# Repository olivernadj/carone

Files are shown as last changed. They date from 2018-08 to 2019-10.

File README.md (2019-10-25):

# CarOne
Turn a self balancing scooter -Hoverboard- into a kids' electric car.

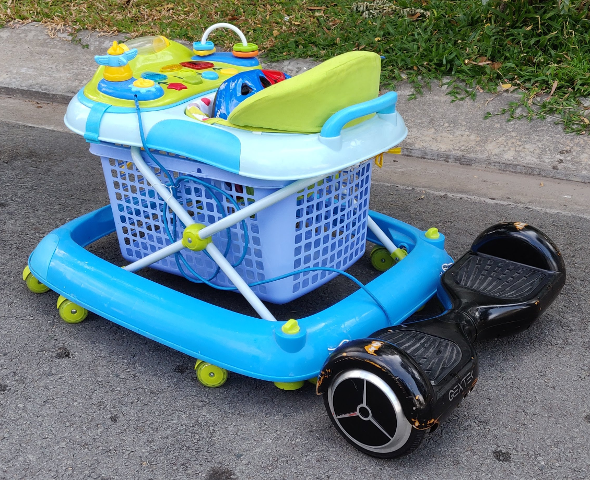
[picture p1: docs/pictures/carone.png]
 

The main goal of the project is to keep the original functionality and behavior of the self balancing scooter, but in the same time with an extension board enable external control. Also use cheap and well know electrical parts and component.

**NOTE: this repo is about to build an Expansion board on top of original Motherboard**
With CarOne Expansion board the max speed you can get is 142cm/s. In case you are not intend to keep the original functionality and you don't mind to replace the firmware and completely re-purpose the hoverboard, I recommend to check this active repo out: https://github.com/NiklasFauth/hoverboard-firmware-hack

## How It Works?
It's follow [Brew's idea][drewsblog] and it hijacks gyro sensor communication between the **Motherboard** and the **Gyro Sensor board**. It sends fake gyro sensor information to **Motherboard**, but also it reads **Hall effect sensor** to detect the speed. 

- [Hardware and wiring](./docs/hardware.md)
- [Board Specification and Applied Units](./docs/specification.md)
- [CarOne glossary](./docs/glossary.md)

## Achievements on Arduino Micro (ATmega328P 16MHz) board.

- [SoftSerialParallelWrite](https://github.com/olivernadj/SoftSerialParallelWrite) for sending parallel UART signal to the Daughterboard.
- Shmitt Trigger in background process.
- [Auto-cruise algorithm](./docs/autocruise.ipynb) development of Auto-cruise algorithm before C implementation.
- All of the above dots in a single board.

## License

    Copyright [2019] [oliver nadj]

    Licensed under the Apache License, Version 2.0 (the "License");
    you may not use this file except in compliance with the License.
    You may obtain a copy of the License at

        http://www.apache.org/licenses/LICENSE-2.0

    Unless required by applicable law or agreed to in writing, software
    distributed under the License is distributed on an "AS IS" BASIS,
    WITHOUT WARRANTIES OR CONDITIONS OF ANY KIND, either express or implied.
    See the License for the specific language governing permissions and
    limitations under the License.

[//]: # (References)
[drewsblog]: http://drewspewsmuse.blogspot.com/2016/06/how-i-hacked-self-balancing-scooter.html

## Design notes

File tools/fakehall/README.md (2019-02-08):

# FakeHall - Fake the hall signal of a hoverboard

Fake the hall project is a testing toll for an other experiment where  I would
like to hijack a hoverboard in a most simple way possible.
It generates fake signal similar to original one, except this use square wave
signal instead of sinusoid one.

## Captured Hall Effect Sensor
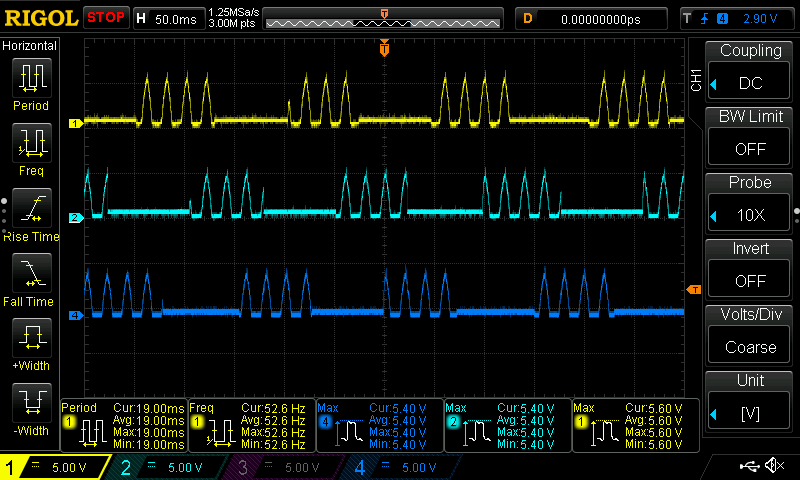
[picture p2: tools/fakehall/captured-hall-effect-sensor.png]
Captured Hall Effect Sensor


## Fake the hall output
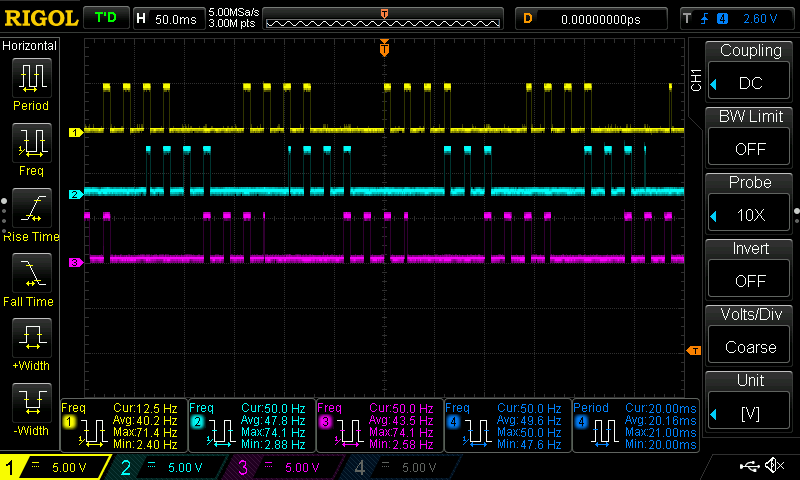
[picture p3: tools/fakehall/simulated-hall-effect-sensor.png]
Fake the hall output


## Demo
IMAGE ALT TEXT HERE (https://youtu.be/ExROV8EL7GM)

## Update
The sinusoid wave come from my broken earth pin in the power strip. What makes the masking features useless.
So I turned the masking features to off by default.

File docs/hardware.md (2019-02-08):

# Hardware and wiring

## Hardware - Expansion Board

### Parts
- 1 x **Arduino Pro Mini** or ATMega328P
- 1 x **LM2596 DC-DC Step Down Buck Converter** Module
- 1 x **74HCT4052N multiplexer** resolver. Can be replaced with discrete logic gates as I did in the earlier version [carone-v3.png](https://raw.githubusercontent.com/olivernadj/carone/master/docs/pictures/carone-v3.png), [data-selector-v3.fzz](https://github.com/olivernadj/carone/raw/master/data-selector-v3.fzz)
- 1 x **AMS1117 3.3 1A Voltage Regulator**
- 4 x 1K, 1 x 10L Resistor
- 2 x 2N2222A NPN Transistor
- 1 x 10nF electrolytic Capacitor
- 4 x 1N4001 Diode - optional

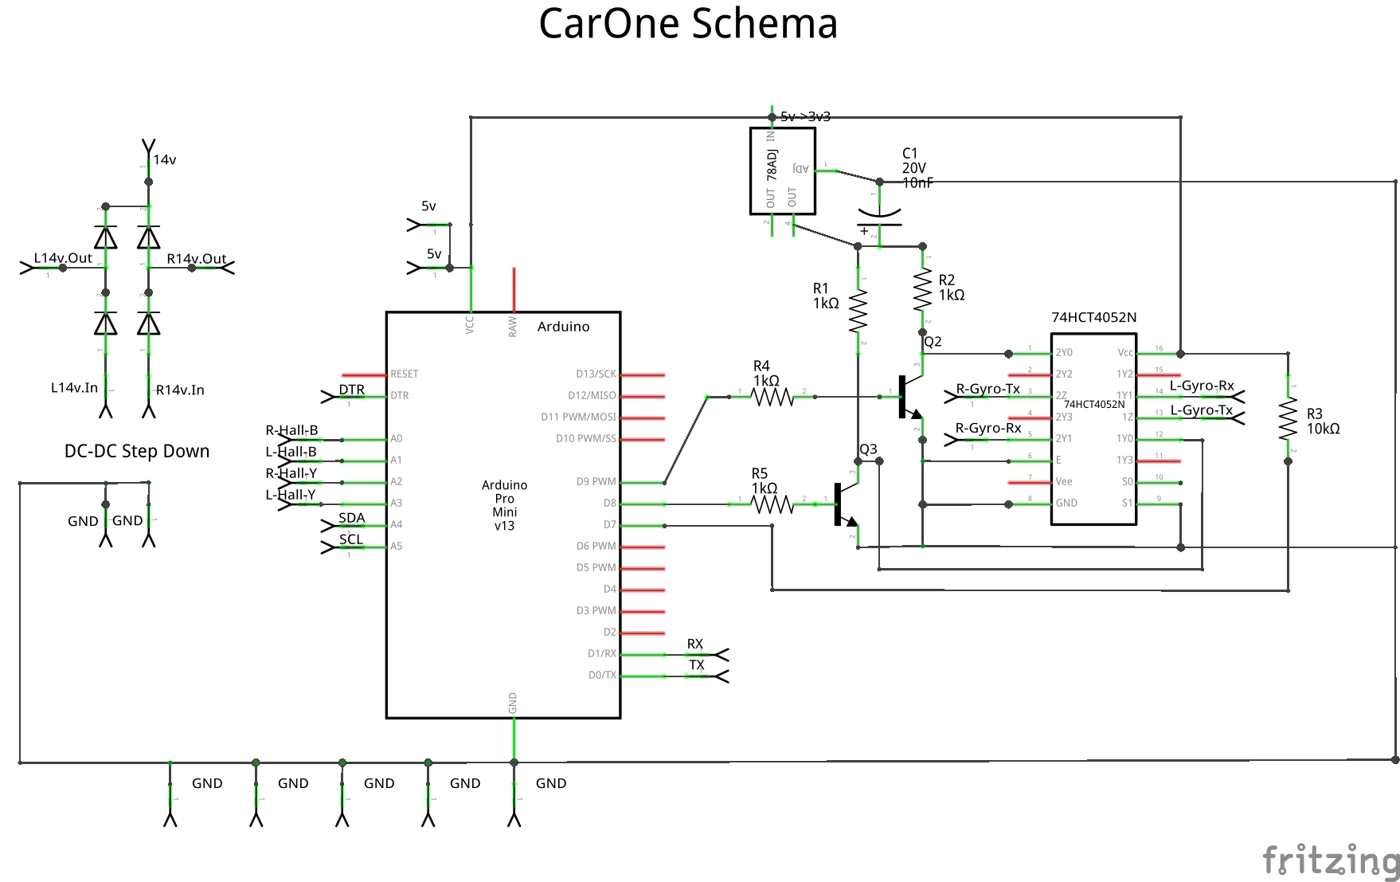
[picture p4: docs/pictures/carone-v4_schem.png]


<p align="center">
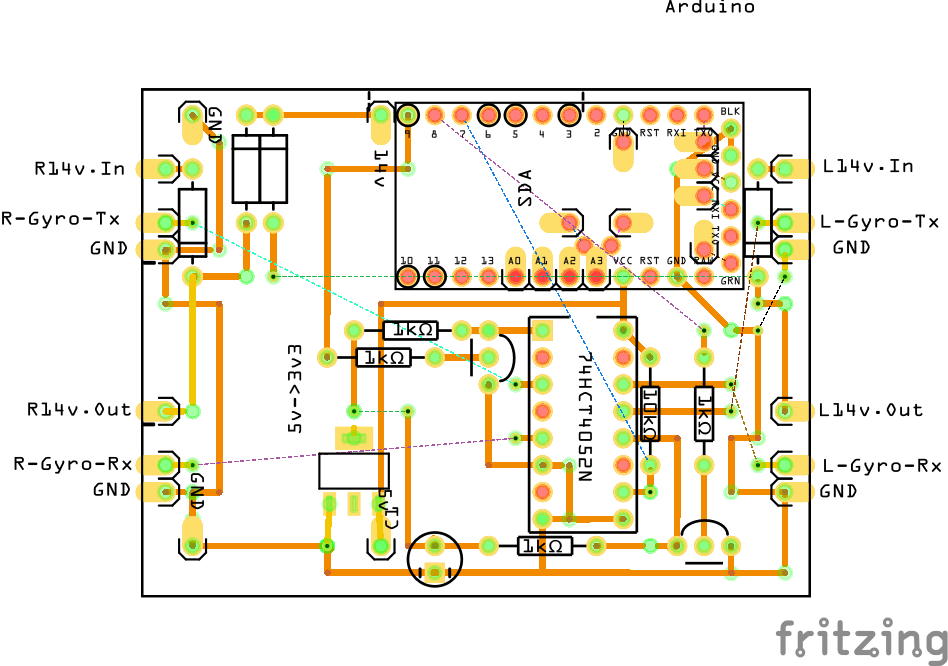
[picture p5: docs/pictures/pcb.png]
  
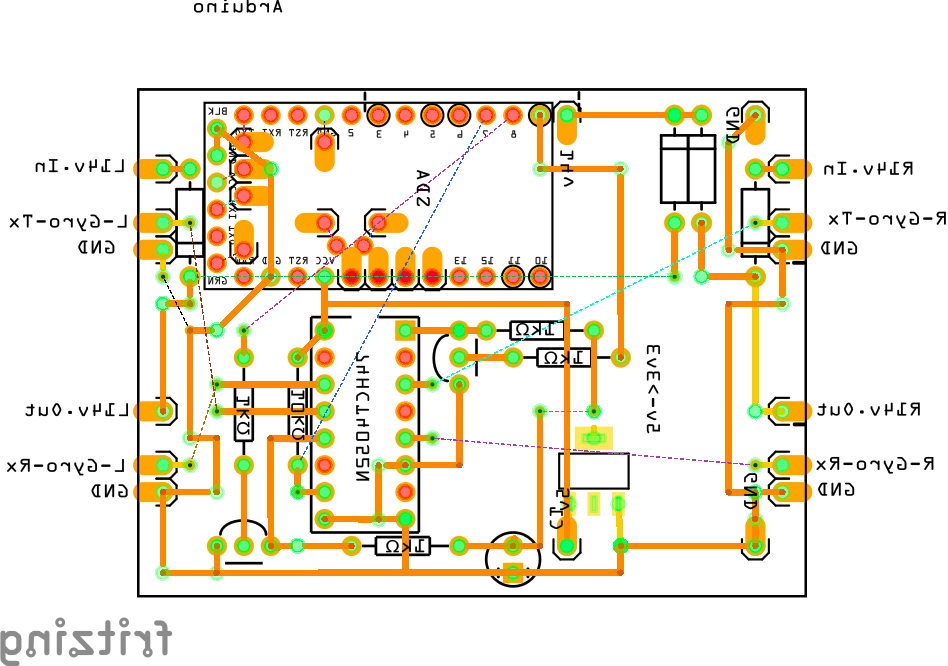
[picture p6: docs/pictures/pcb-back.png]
  
</p>

Check out the Fritzing project file: [carone-v4.fzz](https://github.com/olivernadj/carone/raw/master/carone-v4.fzz)

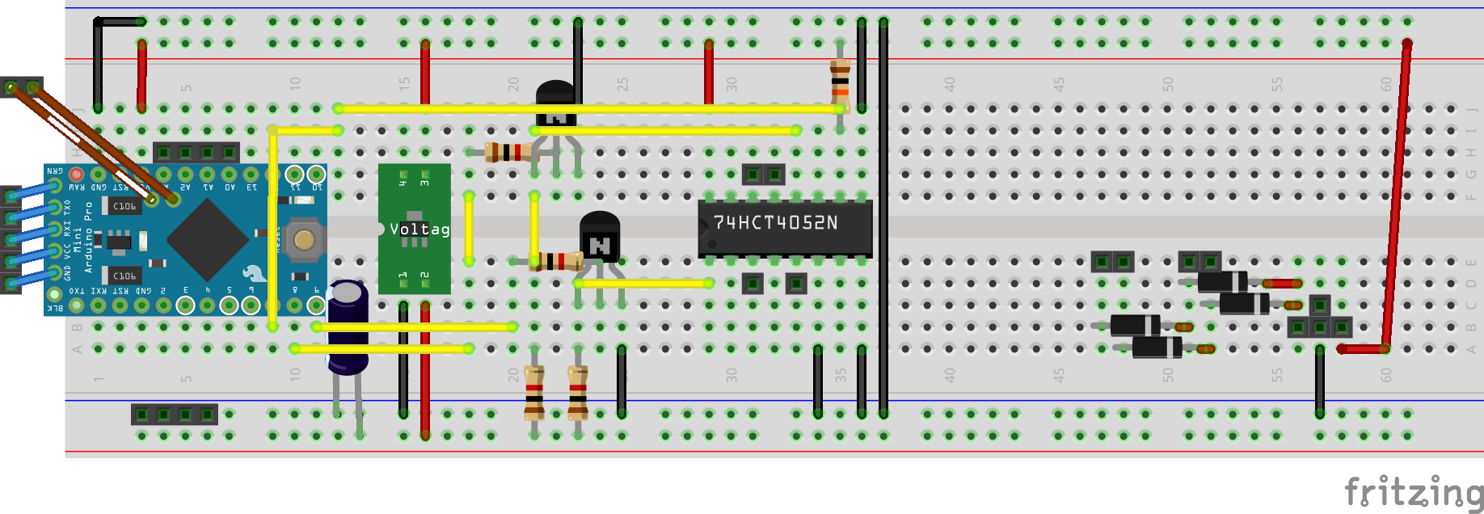
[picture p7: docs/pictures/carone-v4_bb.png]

---

Video: CarOne Expansion Boards Evolution - Try and fail (https://youtu.be/8EtJPLyAzEU)

## How to wire?
The minimum damage you need to do is to cat wires.

<p align="center">
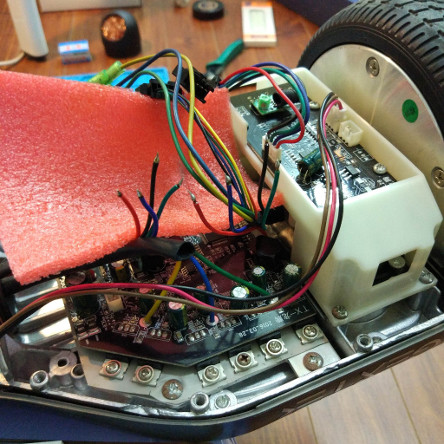
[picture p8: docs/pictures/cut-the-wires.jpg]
  
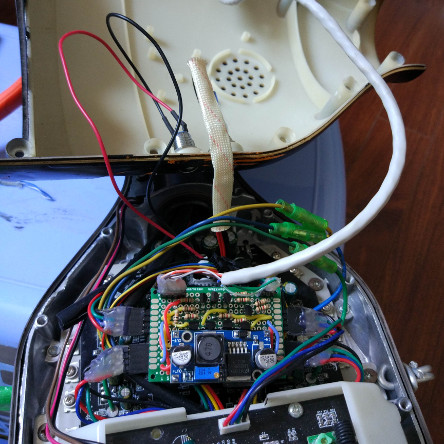
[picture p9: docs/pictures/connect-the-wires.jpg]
  
</p>

Affected wires on both left and right side:
- Hall Yellow and Blue - for speed detection
- Gyro Sensor Red and Black - for power supply to Expansion board
- Gyro Sensor Green - for receiving fake UART from Expansion board

The transmission signal from the Motherboard to Gyro Sensor is untouched.

Abbreviation | Description |  | Abbreviation | Description
--- | --- | --- | --- | ---
**`DTR`** | Arduino Serial Reset | | **`L14v.In`** | Left Red Gyro Sensor from the Motherboard
**`DTR`** | Arduino Serial Reset | | **`R14v.In`** | Right Red Gyro Sensor Red from the Motherboard
**`RX`** | Arduino Serial RX | | **`L14v.Out`** | Left Red Gyro Sensor Red to Gyro Sensor
**`TX`** | Arduino Serial TX | | **`R14v.Out`** | Right Red Gyro Sensor Red to Gyro Sensor
**`L-Hall-B`** | Left Hall Blue - join | | **`L-Gyro-Rx`** | Left Green Gyro Sensor Red from Gyro Sensor
**`L-Hall-Y`** | Left Hall Yellow - join | | **`R-Gyro-Rx`** | Right Green Gyro Sensor Red from Gyro Sensor
**`R-Hall-B`** | Right Hall Blue - join | | **`L-Gyro-Tx`** | Left Green Gyro Sensor Red to the Motherboard
**`R-Hall-Y`** | Right Hall Yellow - join | | **`R-Gyro-Tx`** | Right Green Gyro Sensor Red to the Motherboard

---
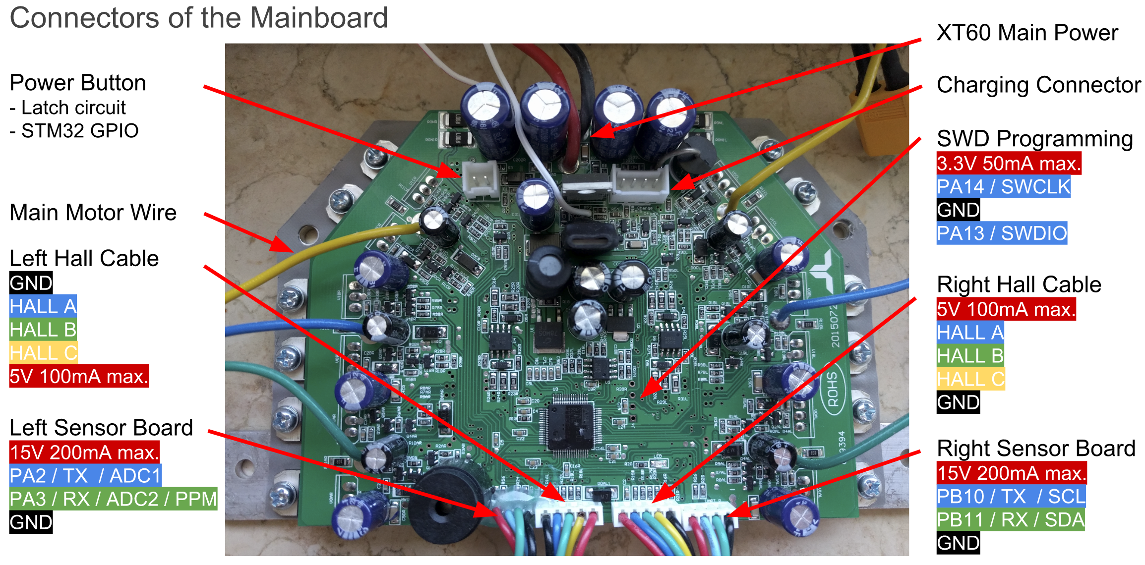
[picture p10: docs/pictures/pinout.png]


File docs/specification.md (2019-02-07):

## Original board Specification
Property | Measured value
--- | ---
Wheel diameter | 17 cm
Wheel circumference | 53.4 cm
Wheel revolution | 15 hall cycles
Max controllable speed | 142 cm/s
Max single side speed | ~300 cm/s

On single side mode with 0 load, around 2.5-3.3 force yields 1 cm/s.

Some examples:

Force | Speed
--- | ---
100 | 28 
150 | 50 
200 | 77
300 | 120

### Conversions
Conversions between common units of speed

Base value | hall cycles/s | RPM | cm/s
--- | --- | --- | ---
**hall cycles** | 1 | 4 | 3.56
**RPM** | 0.25 | 1 | 0.89
**cm/s** | 0.282 | 1.127 | 1

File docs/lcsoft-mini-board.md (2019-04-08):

# Flush Lcsoft Mini Board to become Logic Analyzer and connect to Ubuntu 18.04 Desktop
This is a walk trough guide how to turn a cheep CY7C68013A Development Board
into a Logic Analyzer.

## Other guides in the topic
- This guide is a simplified version of [sigrok's](https://sigrok.org/wiki/Lcsoft_Mini_Board/Info) installation wiki.
- More details about [USB-FX2 EEPROM here](https://www.triplespark.net/elec/periph/USB-FX2/eeprom/), with troubleshooting.
- For Windows you can take a look at [this instructables](https://www.instructables.com/id/FX2LP-CY7C68013A-USB-Dev-Board-Logic-Analyzer/)

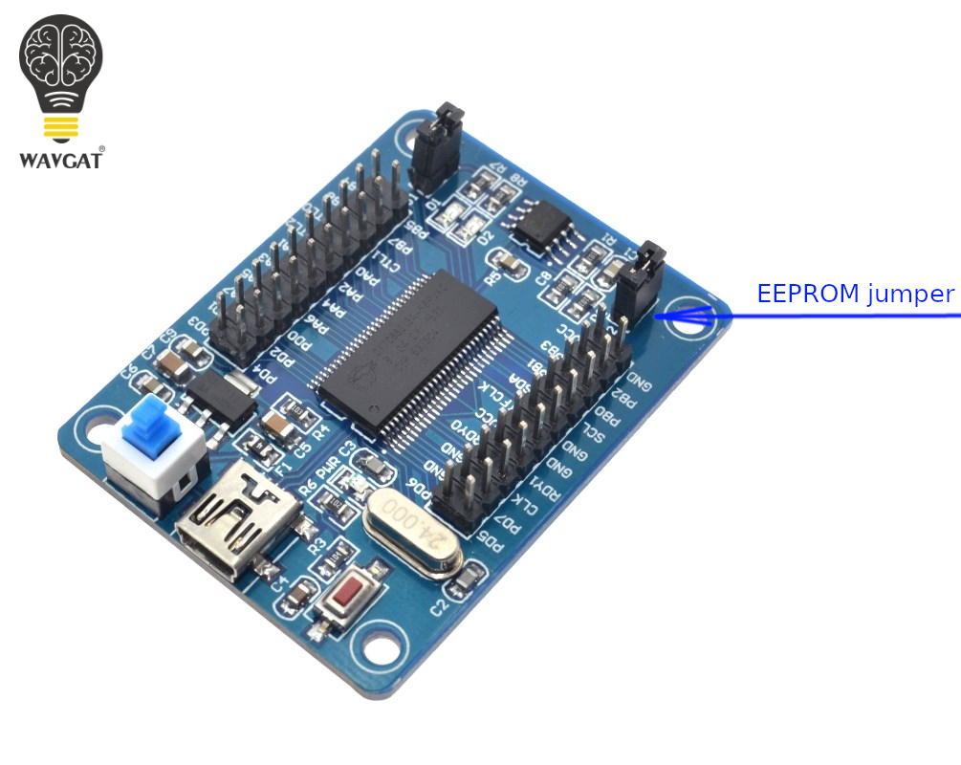
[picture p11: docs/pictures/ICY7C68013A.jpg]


The mini board out of the box is a general programmable board and we have to
tell (flash) it meant to be logic analyzer.

First part of the guide we install necessary packages for flashing. In the last
part we will install packages for connecting the PC to the board.

## Flashing fx2lafw to the EEPROM
Check lsusb output before firmware upload
```
$ lsusb
[...]
Bus 001 Device 025: ID 04b4:8613 Cypress Semiconductor Corp. CY7C68013 EZ-USB FX2 USB 2.0 Development Kit
[...]
```
Tip: you can use `watch lsusb` command to continuously watch the list of USB devices. Easy to catch newly plugged devices.

## Prerequisites
Install `sigrok`, what pulls `pulseview`, `sigrok-cli` and `sigrok-firmware-fx2lafw` packages as well.
```
$ sudo apt install sigrok
```

Check for pre-built firmware file `fx2lafw-cypress-fx2.fw`
```
 ~$ find /usr/ -iname "fx2lafw-cypress-fx2.fw"
/usr/share/sigrok-firmware/fx2lafw-cypress-fx2.fw
```
Although [fxload](https://packages.ubuntu.com/en/source/bionic/all/fxload) can be installed via package manager, it is a wired old version.

Better to download from [triplespark.net](http://www.triplespark.net/elec/periph/USB-FX2/eeprom/fxload-full-2008_10_13-ww3.tar.gz) and compile.
```
$ wget https://raw.githubusercontent.com/olivernadj/carone/master/eeprom/fxload-full-2008_10_13-ww3.tar.gz
$ tar -xzf fxload-full-2008_10_13-ww3.tar.gz
$ cd fxload-2008_10_13
fxload-2008_10_13$ make
cc -c -O -Wall   ezusb.c -o ezusb.o
cc -c -O -Wall   main.c -o main.o
cc -o fxload ezusb.o main.o
```
Download `fx2lafw-cypress-fx2.ihx` from this repository or follow original [install documentation](https://sigrok.org/wiki/Fx2lafw#Build_fx2lafw).

```
fxload-2008_10_13$ wget https://raw.githubusercontent.com/olivernadj/carone/master/eeprom/fx2lafw-cypress-fx2.ihx
```

## Testing the firmware
1. Disconnect the board.
2. Disconnect the EEPROM jumper. The chip will boot from its default bootloader.
3. Connect the board to the computer, and run a simple `sigrok-cli` test.

- If you see a "fx2lafw: Device came back after [some] ms." anywhere in the result, it means the firmware works, and you can proceed.
- If however, you get a "fx2lafw: Device failed to re-numerate." error, STOP. The firmware will not work.

## Flashing the firmware
1. Disconnect the board from the PC, and connect the EEPROM jumper. The board needs to boot from the EEPROM, otherwise `fxload` will not be able to write to the EEPROM.
2. Look at lsusb for the bus and device address.
```
$ lsusb
[...]
Bus 001 Device 029: ID 04b4:8613 Cypress Semiconductor Corp. CY7C68013 EZ-USB FX2 USB 2.0 Development Kit
[...]
```
In this case, the bus is *001* and device is *029*. You will need this information later.
```
fxload-2008_10_13$ ./fxload -D /dev/bus/usb/001/029 -I ./fx2lafw-cypress-fx2.ihx -c 0x01 -s ./Vend_Ax.hex -t fx2
don't see a large enough EEPROM, status=1, val=0 (ignored)
FX2:  config = 0x01, connected, I2C = 400 KHz
Writing vid=0x04b4, pid=0x6473
```
3. Done. Now you can disconnect the board from the computer. Leave the EEPROM jumper connected. The next time you connect the board, it will boot fx2lafw directly, and sigrok will not need to upload the firmware every time it runs.

## Troubleshooting
- _don't see a large enough EEPROM_ - you've may used the package maintained version. Newer `fxload` version ignore this problem.  

## Using and testing

Open `pulseview`. Normally it detects the device. If not choose *fx2lafw* driver and scan for devices.

I used an Arduino as a simple 6-bit binary counter & monitor the output pins 8 to 13.

Connect the GND of the Arduino to GND of the FX2LP.

Connect
- pin 8 of the Arduino to PB0 of the FX2LP,
- pin 9 to PB1
- pin 10 to PB2
- pin 11 to PB3, so on..

bitcounter.ino:
```
int i=0;
void setup() {
  DDRB = B11111;
}
void loop() {
  PORTB = i;
  i++;
  i&=0x1f;
}
```

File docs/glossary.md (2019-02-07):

# CarOne glossary

**Daughterboard** - is an extension of the motherboard of a computer. However, unlike an expansion board, it is not simply another device added to a motherboard to increase its functionality. Instead, it provides the circuitry for an integral function of the motherboard. Without the daughterboard, a motherboard that depends on it will not function. [\[3\]][3]

**Battery** - This battery pack is made of 20pcs Li-ion 18650 battery cells. Rated Voltage: 36V.

**Charger** - 42V 2A Hoverboard Power AC Adapter Charger.

**Expansion board** - is a PCB that fits into an expansion slot on a desktop computer. An expansion card is used to give a computer additional capabilities, such as enhanced video performance via a graphics card. [\[3\]][3]

**Gyro board** - uses UART 9bit, no parity, 1 stop bit for communication with motherboard.

**Hall effect sensor** - is a transducer that varies its output voltage in response to a magnetic field. Hall effect sensors are used for proximity switching, positioning, speed detection, and current sensing applications. [\[8\]][8]

**Hoverboard** - A self-balancing scooter is a personal transporter consisting of two motorized wheels connected to a pair of articulated pads on which the rider places their feet. The rider controls the speed by leaning forwards or backwards, and direction of travel by twisting the pads. [\[6\]][6]

**Logic Level Converter** - bi-directional logic level converter is a small device that safely steps down 5V signals to 3.3V AND steps up 3.3V to 5V at the same time. [\[11\]][11]

**NOT gate** - An inverter circuit outputs a voltage representing the opposite logic-level to its input. Its main function is to invert the input signal applied. [\[1\]][1]

**Motherboard** - is the main printed circuit board (PCB) found in general purpose microcomputers and other expandable systems. It holds and allows communication between many of the crucial electronic components of a system. [\[2\]][2]

**Motor Control Board** - the heart and brain of the smartboard. It is responsible for when and where to throw all that battery power. The main focus of the control board is the six half-H drivers, which drive two 3-phase motors. [\[7\]][7]

**Multiplexer** - In electronics, a multiplexer (or mux) is a device that selects one of several analog or digital input signals and forwards the selected input into a single line. A multiplexer of inputs has select lines, which are used to select which input line to send to the output. [\[10\]][10]

**Printed circuit board (PCB)** - mechanically supports and electrically connects electronic components or electrical components using conductive tracks, pads and other features etched from one or more sheet layers of copper laminated onto and/or between sheet layers of a non-conductive substrate. Components are generally soldered onto the PCB to both electrically connect and mechanically fasten them to it. [\[5\]][5]

**Schematic diagram** - is a circuit which shows the connections in a clear and standardized way. A schematic diagram shows the components and their values and connections in an understandable manner. It is usually used to communicate or intended to convey the connections and working of the circuit to other engineers. [\[4\]][4]

**Schmitt trigger** - In electronics, a Schmitt trigger is a comparator circuit with hysteresis implemented by applying positive feedback to the noninverting input of a comparator or differential amplifier. It is an active circuit which converts an analog input signal to a digital output signal. [\[9\]][9]

**Sisterboard** - if two daughter or expansion boards have a common motherboard, they are sister.

**Step Down Power Module DC-DC Converter** - is an electronic circuit or electromechanical device that converts a source of direct current (DC) from one voltage level to another.

**Voltage regulator** -  is an electronic circuit that provides a stable DC voltage independent of the load current, temperature and AC line voltage variations. A voltage regulator may use a simple feed-forward design or may include negative feedback. It may use an electromechanical mechanism, or electronic components. [\[12\]][12]

**Wheel motor** - brushless DC motor. It takes eight wires to run these: three large power leads for the three phases (controlled by the motor control board), and five leads for the Hall effect sensors that track the rotor’s position. The feedback from those sensors lets those big transistors on the motor control board know when to switch, making for a nice smooth ride. [\[7\]][7]

**Wiring diagram** - is mainly intended to convey the wiring or connection between the components in a proper way without any confusion, so that one can create a prototype easily using that. [\[5\]][5]

---
### References
\[1\]: https://en.wikipedia.org/wiki/Inverter_(logic_gate)
\[2\]: https://en.wikipedia.org/wiki/Motherboard
\[3\]: https://www.quora.com/In-computers-is-there-a-daughter-board-or-a-sister-board
\[4\]: https://www.quora.com/What-is-the-difference-between-schematic-diagram-and-wiring-diagram-for-electrical-connections
\[5\]: https://en.wikipedia.org/wiki/Printed_circuit_board
\[6\]: https://en.wikipedia.org/wiki/Self-balancing_scooter
\[7\]: https://ifixit.org/blog/7821/swagway-teardown-hoverboards/
\[8\]: https://en.wikipedia.org/wiki/Hall_effect_sensor
\[9\]: https://en.wikipedia.org/wiki/Schmitt_trigger
\[10\]: https://en.wikipedia.org/wiki/Multiplexer
\[11\]: https://www.sparkfun.com/products/12009
\[12\]: https://en.wikipedia.org/wiki/Voltage_regulator

[//]: # (References)
[1]: https://en.wikipedia.org/wiki/Inverter_(logic_gate)
[2]: https://en.wikipedia.org/wiki/Motherboard
[3]: https://www.quora.com/In-computers-is-there-a-daughter-board-or-a-sister-board
[4]: https://www.quora.com/What-is-the-difference-between-schematic-diagram-and-wiring-diagram-for-electrical-connections
[5]: https://en.wikipedia.org/wiki/Printed_circuit_board
[6]: https://en.wikipedia.org/wiki/Self-balancing_scooter
[7]: https://ifixit.org/blog/7821/swagway-teardown-hoverboards/
[8]: https://en.wikipedia.org/wiki/Hall_effect_sensor
[9]: https://en.wikipedia.org/wiki/Schmitt_trigger
[10]: https://en.wikipedia.org/wiki/Multiplexer
[11]: https://www.sparkfun.com/products/12009
[12]: https://en.wikipedia.org/wiki/Voltage_regulator

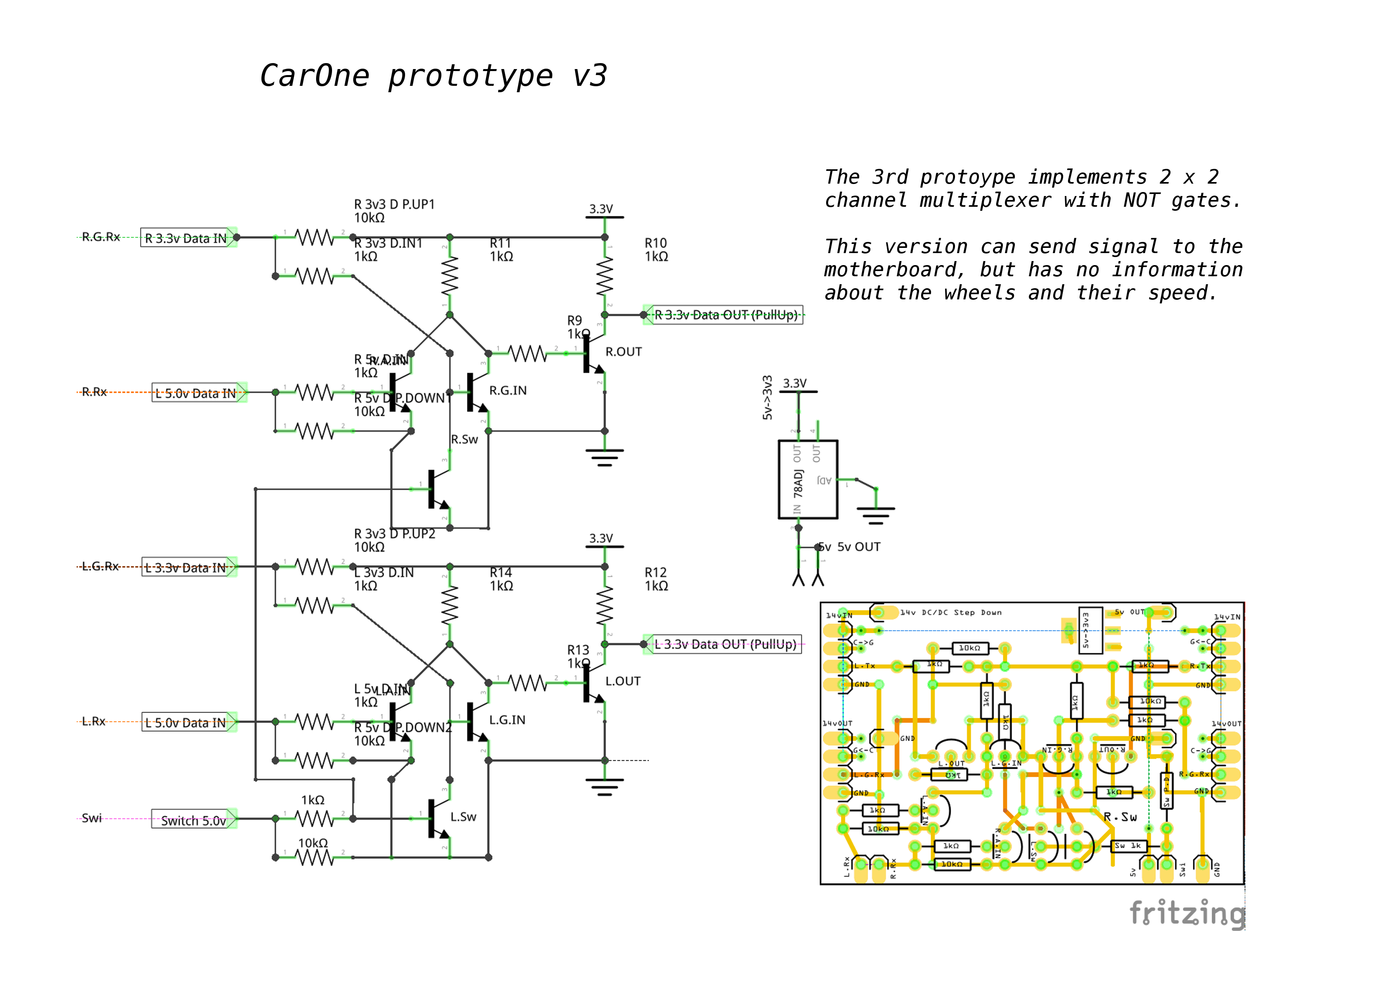
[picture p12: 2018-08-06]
docs/pictures/carone-v3.png

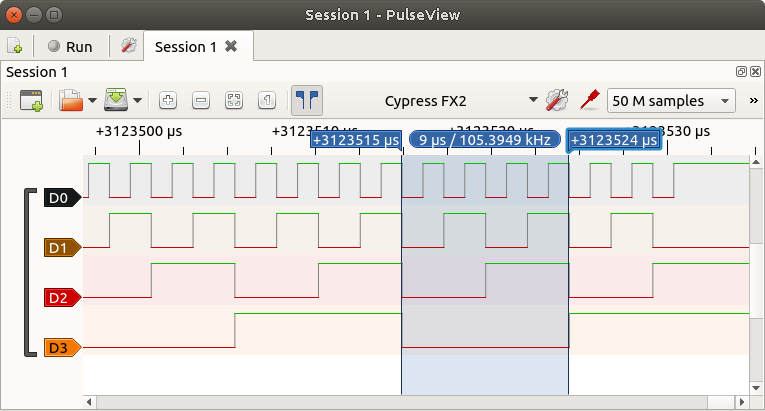
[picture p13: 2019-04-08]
docs/pictures/pulseview.png

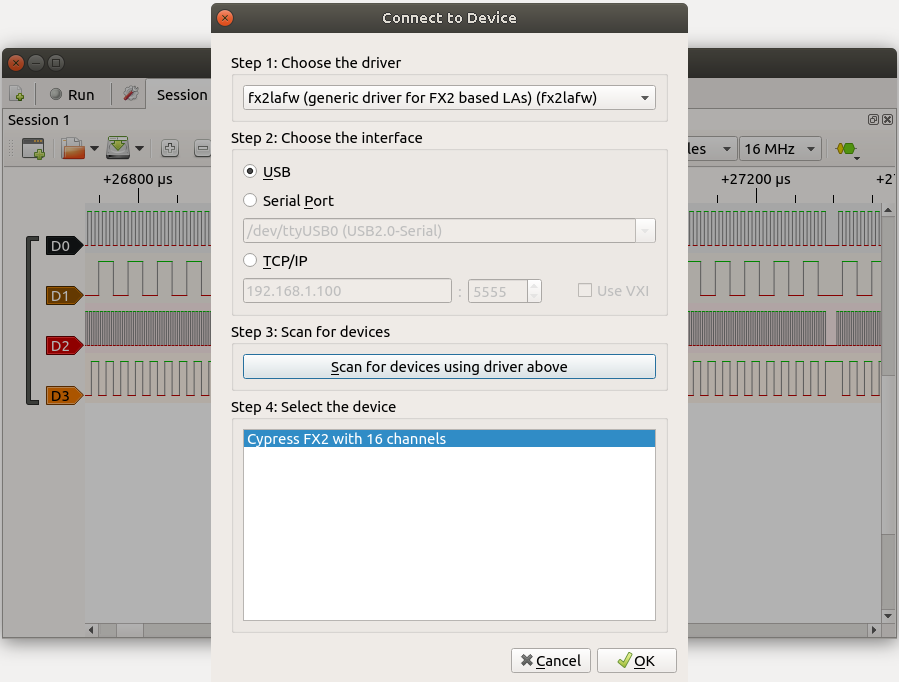
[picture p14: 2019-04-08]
docs/pictures/pulseview-device.png

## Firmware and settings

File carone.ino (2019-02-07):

#include <SoftSerialParallelWrite.h> // SoftSerialParallelWrite library for parallel UART transmission.
#include <Wire.h> // I2C Wire library.

// A4 and A5 can be used for debug purpose only if not used for I2C. The debug signal can be read by digital analyzer or oscilloscope.
#define _DEBUG 0

// Baud-rate, frame size and timing for UART communication between gyro-daughterboard and motherboard .
#define _GYRO_SERIAL 26275 //Baud-rate.
#define _GYRO_FRAMES 10 // Number of frames in one batch.
#define _GYRO_FRAME_LENGTH 450 // Frame length. UART transmission omits stop bits to save time for ATmega328 core. Otherwise poor core, have to spend all the resources to deliver UARD bytes.
#define _GYRO_FRAMES_LENGTH 875 // Frame length + delay between batch.
// Example:
//   Short 450 us frame cycles (time between 2 start bit) happen 10/9 times.
//   Long 875 us cycles (time between 2 start bit) happen 10/1 times.

// Optional Arduino serial for debugging and controlling.
#define _SERIAL_CTRL 9600 // bandwidth or 0 means disabled.
#define _SERIAL_TIMEOUT 5 // Time limits for reading serial inputs in millis. Unfortunately sometimes 5 millis not enough, but with longer time limit there would be not enough time between UART frames.
#define _SERIAL_INFO 1 // Serial var dump is time expensive. Not recommended in production.

// Optional I2C settings. NOTICE: it uses the same pins - A4, A5 like signal debug .
#define _I2C_CTRL 1//1 // 1 means enabled or 0 means disabled.
#define _I2C_BUS_ADDRESS 8

#if _DEBUG && _I2C_CTRL // Throw compile error if both pin debug and I2C enabled.
the_debug_use_the_same_pins_as_I2C_therefore_both_cannot_be_used;
#endif

// ===========+=== SETTINGS FOR DRIVING MECHANISM ============================//
// This settings are basically fine tuning to an instance of hover board.
// Here you can change the driving dynamic, sensors logic, etc.
//
// Default directing mode
#define _DEFAULT_DIRECTION 0 // 0:acceleration, 1:target speed.
// BTW: The measured output from gyro board at ~30 degree horizontal angle is 2900.
#define _MAX_GYRO_ACCELERATION 180 // Absolute upper limit for acceleration all across the system.
#define _AUTOCRUISE_SINGLE_START_FORCE 80 // Initial force. With 0 initial force the acceleration is sluggish. Single mode means only one wheel is working and the acceleration force related to speed is linear.
#define _AUTOCRUISE_SINGLE_FORCE_INC 5 // Force adjusting increments or decrements.
#define _AUTOCRUISE_DUAL_START_FORCE 60 // Initial force. Dual mode means both wheels are working and the acceleration happens exponentially, therefor need to converge to zero. Zero force means keep velocity.
#define _AUTOCRUISE_DUAL_FORCE_INC 10 // Force adjusting increments or decrements. Only used for acceleration from 0 speed.
#define _AUTOCRUISE_DUAL_BASE_ACC 24 // cm/s^2; Max speed 142cm/s in 6 second
#define _AUTOCRUISE_DUAL_ADVANCE 1 // second; Used for calculate future speed and acceleration
#define _AUTOCRUISE_DUAL_ADVANCE_RECIPROCAL (1/_AUTOCRUISE_DUAL_ADVANCE) // not really used, keep it integer due to better performance
// Maximum allowed speed before the safety parking mode activated.
// The hover board tend to loose control above that speed.
#define _MAX_SPEED 142 // Max controllable speed in cm/s. More about units in README.md
#define _SAFETY_SPEED_LIMIT 150 // Force parking mode above that speed. 
// Settings for hall sensor of the wheel.
#define _HALL_DIRECTION_DETECT_LIMIT 120 // Detects direction (cw,ccw) under this wheel cm/s limit.
// Although ccw status logically is a boolean, we need to avoid hall check errors. The implemented software solution is to incrementally enforcing the status on each sampling. This method absorbs occasional sampling errors.
#define _HALL_CLOCKWISE_PROBABILITY_CW 2 // Maximum cw enforcement. Example: ccw: -3, -2, -1; cw: 0, 1, 2
#define _HALL_CLOCKWISE_PROBABILITY_CCW -3 // Maximum cw enforcement. Example: ccw: -3, -2, -1; cw: 0, 1, 2

// =========== END OF SETTINGS FOR DRIVING MECHANISM =========================//

SoftSerialParallelWrite  mySerial(2); // register 2 lower ports of PORTB for parallel UART transmission
const int debugPin2            =  A5; // Used for Debug only if _DEBUG enabled
const int debugPin1            =  A4; // Used for Debug only if _DEBUG enabled
const int inputSelector        =   7; // Hijack gyro sensor communication. It controls the source for multiplexer (gyro-daughterboard VS CarOne).
const int rightHallBluePin     =  A0; // Hall effect direction check.
const int leftHallBluePin      =  A1; // Same as above, but for the left wheel.
const int rightHallYellowPin   =  A2; // Hall effect triggering, as interrupt.
const int leftHallYellowPin    =  A3; // Same as above, but for the left wheel.
const int shmittTriggerUpper   = 450; // (1025 / 5) * 2.2V
const int shmittTriggerMiddle  = 337; // (1025 / 5) * 1.65V
const int shmittTriggerLower   = 225; // (1025 / 5) * 1.1V

uint8_t rightHallBlueState;
uint8_t leftHallBlueState;
uint8_t rightHallYellowState;
uint8_t leftHallYellowState;

signed long leftLastRealInterrupt  = 0; // when did the last hall interrupt happened.
signed long rightLastRealInterrupt = 0; // Same as above, but for the right wheel.
signed int leftActualCmPS          = 0; // Measured Absolute wheel speed in cm/s unit. More about units in README.md
signed int rightActualCmPS         = 0; // Same as above, but for the right wheel
signed int leftActualAcc           = 0; // Measured acceleration in cm/s^2 unit. More about units in README.md
signed int rightActualAcc          = 0; // Same as above, but for the right wheel
signed int leftForce               = 0; // Accelerating force. A wired unit what gyro extension board sends to motherboard based on its horizontal angle.
signed int rightForce              = 0; // Same as above, but for the right side
signed int leftTargetCmPS          = 0; // Target speed (wheel RMP) in auto-cruise direction mode
signed int rightTargetCmPS         = 0; // Same as above, but for the right wheel
signed int leftClockwise           = 0; // Example: ccw: -3, -2, -1; cw: 0, 1, 2
signed int rightClockwise          = 0; // Example: ccw: -3, -2, -1; cw: 0, 1, 2

char command = 'n'; //last received input by serial. n is no acceleration
char shifter = 'P'; // [P]ark or [D]rive
bool leftDrive = false; // Used for single wheel control
bool rightDrive = false; // Same as above

enum directions {Acceleration, Autocruise} directedby = _DEFAULT_DIRECTION;

volatile byte i2cReg = 0xFF; // Storage for I2C internal register address.

/**
 * Debugging
 *
 * This function generates a brief pulse
 * for debugging or measuring on an oscilloscope.
 * Example:
 *   debugPulse(debugPin1, 1); // expected signal on pin1: __|__
 *   debugPulse(debugPin2, 3); // expected signal on pin2: __|_|_|__
 */
#if _DEBUG
inline void debugPulse(uint8_t pin, uint16_t count) {
  bool pinStatus = digitalRead(pin);
  while (count--) {
    digitalWrite(pin, 1 ^ pinStatus);
    digitalWrite(pin, pinStatus);
  }
}
#else
inline void debugPulse(uint8_t, uint16_t) {}
#endif

#define cbi(sfr, bit) (_SFR_BYTE(sfr) &= ~_BV(bit)) // Macro Set bit in IO port port.
#define sbi(sfr, bit) (_SFR_BYTE(sfr) |= _BV(bit)) // Macro Clear bit in IO port port.

/**
 * Trigger an analog read background task for given pin.
 */
bool analogReadStart(uint8_t pin) {
  if (ADCSRA & (1<<ADSC)) {
    return false; // return false if ADC is busy
  }
  if (pin >= 14) pin -= 14; // allow for channel or pin numbers
  // set the analog reference (high two bits of ADMUX) and select the
  // channel (low 4 bits).  this also sets ADLAR (left-adjust result)
  // to 0 (the default).
  ADMUX = (1<<REFS0)| (pin & 0x07);
  // start the conversion
  sbi(ADCSRA, ADSC);
  return true;
}

/**
 * Reads the result from analog measurement done in background.
 */
int analogReadResult() {
  uint8_t low, high;
  // ADSC is cleared when the conversion finishes
  while (ADCSRA & (1<<ADSC));
  // we have to read ADCL first; doing so locks both ADCL
  // and ADCH until ADCH is read.  reading ADCL second would
  // cause the results of each conversion to be discarded,
  // as ADCL and ADCH would be locked when it completed.
  low  = ADCL;
  high = ADCH;
  // combine the two bytes
  return (high << 8) | low;
}

/**
 * Transmits imitated UART signal, just like gyro sensor does.
 * Uses SoftSerialParallelWrite library what enables to do multiple UART
 * transmission with same frame size and baud-rate
 *
 * ATTENTION: the logical high and low has been inverted (to be align with NOT
 * gate on logic level shift from 5v to 3.3v)
 */
void writeCurrentSpeed() {
  if (digitalRead(inputSelector) == HIGH) {
    mySerial.write(~0, ~0);
  } else {
    //0xC00 2 stop bits and <<1 for the start
    const uint16_t startSignal = 0xFC00 | (256 << 1);
    const uint16_t driveEndSignal = 0xFC00 | (85 << 1);
    const uint16_t parkEndSignal = 0xFC00 | (170 << 1);

    static unsigned int currentFrame = 6;
    static uint16_t leftEndSignal = parkEndSignal;
    static uint16_t rightEndSignal = parkEndSignal;
    static uint16_t leftForceLowFrame;
    static uint16_t leftForceHighFrame;
    static uint16_t rightForceLowFrame;
    static uint16_t rightForceHighFrame;

    switch (currentFrame) {
      case 1:
        mySerial.write(~startSignal, ~startSignal);
        leftForceLowFrame = 0xFC00 | ((-leftForce & 0xFF) << 1); // Apply invert logic
        leftForceHighFrame = 0xFC00 | (((-leftForce >> 8) & 0xFF) << 1); // Apply invert logic
        rightForceLowFrame = 0xFC00 | ((rightForce & 0xFF) << 1);
        rightForceHighFrame = 0xFC00 | (((rightForce >> 8) & 0xFF) << 1);
        if (shifter == 'D') {
          if (directedby == Autocruise) {
            leftEndSignal = (leftDrive) ? driveEndSignal : parkEndSignal ;
            rightEndSignal = (rightDrive) ? driveEndSignal : parkEndSignal ;
          } else {
            leftEndSignal = driveEndSignal;
            rightEndSignal = driveEndSignal;
          }
        } else {
          leftEndSignal = parkEndSignal;
          rightEndSignal = parkEndSignal;
        }
        currentFrame++;
        break;
      case 2:
      case 4:
        mySerial.write(~rightForceLowFrame, ~leftForceLowFrame);
        currentFrame++;
        break;
      case 3:
      case 5:
        mySerial.write(~rightForceHighFrame, ~leftForceHighFrame);
        currentFrame++;
        break;
      case 6:
        mySerial.write(~rightEndSignal, ~leftEndSignal);
        currentFrame = 1;
        break;
    }
  }
}

/**
  * Calculates actual acceleration
  * 
  * !IMPORTANT this method must be called in every 50 millis.
  * 
  * To avoid expensive division it has been called in every 50 millis, therefore 
  * the time become multiply of 20; 1s / 0.05 => 20;
  * The latest two period has 8 and the 3rd last has 4 multiplication.
  */
void calculateActualAcceleration() {
  static signed int lV1 = 0, lV2 = 0, lV3 = 0;
  static signed int rV1 = 0, rV2 = 0, rV3 = 0;
  leftActualAcc  = ((leftActualCmPS  - lV3) * 8) + ((lV3 - lV2) * 8) + ((lV2-lV1) * 4);
  rightActualAcc = ((rightActualCmPS - rV3) * 8) + ((rV3 - rV2) * 8) + ((rV2-rV1) * 4);
  lV1 = lV2;
  lV2 = lV3;
  lV3 = leftActualCmPS;
  rV1 = rV2;
  rV2 = rV3;
  rV3 = rightActualCmPS;
}

/**
  * Calculates necessary force to catch up with target speed 
  * 
  * Only called if both wheel are operating
  */
void calculateDualAutocruise() { //called in every 100ms
  signed int leftVf = 0; //future velocity
  signed int leftAt = 0; //target acceleration
  signed int leftForceInc = 0;
  signed int rightVf = 0; //future velocity
  signed int rightAt = 0; //target acceleration
  signed int rightForceInc = 0;
  static signed int rightLastTargetCmPS = 0; // For applying initial force if target speed has changes;
  static signed int leftLastTargetCmPS = 0; // For applying initial force if target speed has changes;

  leftDrive = true;
  rightDrive = true;

  leftForceInc =  (leftLastTargetCmPS != leftTargetCmPS ? _AUTOCRUISE_DUAL_START_FORCE : _AUTOCRUISE_DUAL_FORCE_INC);
  leftVf = leftActualCmPS + (_AUTOCRUISE_DUAL_ADVANCE * leftActualAcc);
  if (leftTargetCmPS == leftVf) {
    leftAt = 0;
  } else if ( (leftActualAcc > 0 && leftVf > leftTargetCmPS) || (leftActualAcc < 0 && leftVf < leftTargetCmPS) ) {
    leftAt = (leftTargetCmPS - leftVf) * _AUTOCRUISE_DUAL_ADVANCE_RECIPROCAL;
  } else {
    leftAt = _AUTOCRUISE_DUAL_BASE_ACC * ( leftTargetCmPS < leftActualCmPS ? -1 : 1 );
  }
  if (leftAt != leftActualAcc) {
    if (leftAt < leftActualAcc) {
      leftForce -= leftForceInc;
    } else {
      leftForce += leftForceInc;
    }
  }
  leftLastTargetCmPS = leftTargetCmPS;

  rightForceInc =  (rightLastTargetCmPS != rightTargetCmPS ? _AUTOCRUISE_DUAL_START_FORCE : _AUTOCRUISE_DUAL_FORCE_INC);
  rightVf = rightActualCmPS + (_AUTOCRUISE_DUAL_ADVANCE * rightActualAcc);
  if (rightTargetCmPS == rightVf) {
    rightAt = 0;
  } else if ( (rightActualAcc > 0 && rightVf > rightTargetCmPS) || (rightActualAcc < 0 && rightVf < rightTargetCmPS) ) {
    rightAt = (rightTargetCmPS - rightVf) * _AUTOCRUISE_DUAL_ADVANCE_RECIPROCAL;
  } else {
    rightAt = _AUTOCRUISE_DUAL_BASE_ACC * ( rightTargetCmPS < rightActualCmPS ? -1 : 1 );
  }
  if (rightAt != rightActualAcc) {
    if (rightAt < rightActualAcc) {
      rightForce -= rightForceInc;
    } else {
      rightForce += rightForceInc;
    }
  }
  rightLastTargetCmPS = rightTargetCmPS;

}

/**
  * Calculates necessary force to catch up with target speed 
  * 
  * Only called if only on wheel is operating
  */
void calculateSingleAutocruise() {
  if (rightDrive == false && leftTargetCmPS != 0) {
    if (leftDrive == false) {
      // always start the drive mode with 0 force
      leftDrive = true;
      leftForce = 0;
    } else if (leftForce == 0) {
      leftForce = (leftTargetCmPS < 0 ? -_AUTOCRUISE_SINGLE_START_FORCE : _AUTOCRUISE_SINGLE_START_FORCE); // initial force
    } else {
      if (leftTargetCmPS > leftActualCmPS) {
        leftForce += _AUTOCRUISE_SINGLE_FORCE_INC; // need to be fine tuned
      } else if(leftTargetCmPS < leftActualCmPS) {
        leftForce -= _AUTOCRUISE_SINGLE_FORCE_INC;
      }
    }
  } else {
    if (leftForce == 0) {
      leftDrive = false;
    } else {
      leftForce = 0;
    }
  }
  if (leftDrive == false && rightTargetCmPS != 0) {
    if (rightDrive == false) {
      rightDrive = true;
      rightForce = 0;
    } else if (rightForce == 0) {
      rightForce = (rightTargetCmPS < 0 ? -_AUTOCRUISE_SINGLE_START_FORCE : _AUTOCRUISE_SINGLE_START_FORCE); // initial force
    } else {
      if (rightTargetCmPS > rightActualCmPS) {
        rightForce += _AUTOCRUISE_SINGLE_FORCE_INC;
      } else if(rightTargetCmPS < rightActualCmPS) {
        rightForce -= _AUTOCRUISE_SINGLE_FORCE_INC;
      }
    }
  } else {
    if (rightForce == 0) {
      rightDrive = false;
    } else {
      rightForce = 0;
    }
  }
}

/**
  * Calculates necessary force to catch up with target speed
  *
  */
void calculateAutocruise() {
  static bool onMyWay = false;
  if (shifter != 'D') {
    leftForce = 0;
    rightForce = 0;
    onMyWay = false;
    leftDrive = false;
    rightDrive = false;
  } else if (!onMyWay && (leftTargetCmPS == 0 || rightTargetCmPS == 0)) { // singe side mode
    calculateSingleAutocruise();
  } else if (onMyWay || (leftTargetCmPS != 0 && rightTargetCmPS != 0)) {
    onMyWay = true;
    calculateDualAutocruise();
  }
  if (leftForce > _MAX_GYRO_ACCELERATION) leftForce = _MAX_GYRO_ACCELERATION;
  if (leftForce < -_MAX_GYRO_ACCELERATION) leftForce = -_MAX_GYRO_ACCELERATION;
  if (rightForce > _MAX_GYRO_ACCELERATION) rightForce = _MAX_GYRO_ACCELERATION;
  if (rightForce < -_MAX_GYRO_ACCELERATION) rightForce = -_MAX_GYRO_ACCELERATION;
}

/**
 * Sets the speed to 0 if no hall interruption for a given period.
 * Applies safety brake when unleashed. - "Normally" the hoverboard looses 
 * control above 140 cm/s and accelerates to max speed uncontrollable  
 */
void speedCheck() {
  signed long currentMillis = millis();
  if (currentMillis - leftLastRealInterrupt > 890) {
    leftActualCmPS = 0;
  }
  if (currentMillis - rightLastRealInterrupt > 890) {
    rightActualCmPS = 0;
  }
  static bool safetyReady = false;
  if (shifter == 'D' && (abs(leftActualCmPS) > _SAFETY_SPEED_LIMIT || abs(rightActualCmPS) > _SAFETY_SPEED_LIMIT)) {
    if (safetyReady) { // apply safety break only for 2 consecutive speed violation
      shifter = 'P';
      if (_SERIAL_CTRL && _SERIAL_INFO) {
        Serial.print("[P] forced; exceed _SAFETY_SPEED_LIMIT:");
        Serial.print(_SAFETY_SPEED_LIMIT);
        Serial.print(";l");
        Serial.print(leftActualCmPS);
        Serial.print(";r");
        Serial.print(rightActualCmPS);
        Serial.println("cm/s;");
      }
    } else {
      safetyReady = true;  // 1st violation gracefully ignored
    }
  } else {
    safetyReady = false;
  }
}
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
void loop() {
  static unsigned long pmTx =  0;
  static unsigned long pmSchmittTrigger =  0;
  static unsigned long pmSpeedCheck =  0;
  static unsigned long pmActualAcceleration =  0;
  static unsigned long pmAutocruise =  0;
  static unsigned long pmListenControl =  0;
  static unsigned long pmSerialInfo =  0;
  static unsigned int txLength = _GYRO_FRAME_LENGTH;
  static unsigned int txCounter = 0;
  unsigned long currentMicros = micros();
  signed long microsTillNextTx = 0;

  // transmissions, just like gyro sensor does
  if (currentMicros - pmTx >= txLength) {
    pmTx = currentMicros;
    writeCurrentSpeed();
    txLength = (++txCounter % _GYRO_FRAMES == 0)
      ? _GYRO_FRAMES_LENGTH : _GYRO_FRAME_LENGTH;
    return;
  } else {
    microsTillNextTx = pmTx + txLength - currentMicros;
  }

  if (currentMicros - pmSchmittTrigger >= 380
      && microsTillNextTx > 25) {  //it takes ~16us-37us on 16MHz
    schmittTrigger();
    pmSchmittTrigger = currentMicros;
    return;
  }

  if (currentMicros - pmSpeedCheck >= 200000
      && microsTillNextTx > 25) {  //it takes ~16us on 16MHz
    pmSpeedCheck = currentMicros;
    speedCheck();
    return;
  }

  if (currentMicros - pmActualAcceleration >= 50000
      && microsTillNextTx > 25) { // it takes ?? on 16MHz
    pmActualAcceleration = currentMicros;
    calculateActualAcceleration();
    return;
  }

  if (directedby == Autocruise && currentMicros - pmAutocruise >= 100000
      && microsTillNextTx > 25) { // it takes ~20us on 16MHz
    pmAutocruise = currentMicros;
    // debugPulse(debugPin2, 3);
    calculateAutocruise();
    // debugPulse(debugPin2, 4);
    return;
  }

  if (_SERIAL_CTRL) {
    if (microsTillNextTx > 50) {
      listenSerialControl();
    }
    if (_SERIAL_INFO && currentMicros - pmSerialInfo >= 2000000
      && microsTillNextTx > 200) { //it takes ~420us on 16MHz
      pmSerialInfo = currentMicros;
      serialInfo();
      return;
    }
  }
}

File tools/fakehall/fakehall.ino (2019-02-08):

#include <pt.h>  // protothread library

static struct pt pt1, pt2, pt3, pt4, pt5; // each protothread needs one of these

#define _SERIAL_DEBUG 9600 // bandwidth or 0 means turned off

const int ledPin = 13;

const int hallYellowPin = 12;
const int hallBluePin = 11;
const int hallGreenPin = 10;

const int waveGenPin = 9;
const int waveMaskSWPin = 8;

const int rotaryEncSWPin = 7;
const int rotaryEncDTPin = 6;
const int rotaryEncCLKPin = 2;

const int maxSpeed = 100; // basically abs(100)

volatile int speed = 0;

int maskSWLastState;
int rotarySWLastState;

bool applyMask = false; // managed by switch
bool maskStateHigh = true;

long blinkLenght = 1000000;
volatile long hallSignLength = 1000000;

bool hallYellowState = true;
bool hallBlueState = true;
bool hallGreenState = false;

/***
  * Periodically checks the states of the switch buttons.
  */
void checkSwitches() {
  int maskSWState;
  int rotarySWState;
  maskSWState = digitalRead(waveMaskSWPin);
  rotarySWState = digitalRead(rotaryEncSWPin);
  if (maskSWState != maskSWLastState && !maskSWState) {
    applyMask ^= 1;
  }
  if (rotarySWState != rotarySWLastState && !rotarySWState) {
    speed = 0;
  }
  maskSWLastState = maskSWState;
  rotarySWLastState = rotarySWState;
}

/***
  * A protothread helper function calls checkSwitches after 'interval' microseconds passed
  */
static int ptCheckSwitches(struct pt *pt, unsigned long interval) {
  static unsigned long timestamp = 0;
  if (timestamp > micros()) timestamp = micros();
  PT_BEGIN(pt);
  while(1) {
    PT_WAIT_UNTIL(pt, micros() - timestamp > interval );
    timestamp = micros();
    checkSwitches();
  }
  PT_END(pt);
}

/***
  * Hall effect signal generator
  */
void hallSingGen() {
  if (speed > 0) {
    if (hallYellowState == hallBlueState) {
      hallYellowState ^= 1;
    } else if (hallBlueState == hallGreenState) {
      hallBlueState ^= 1;
    } else if (hallGreenState == hallYellowState) {
      hallGreenState ^= 1;
    }
  } else if (speed < 0) {
    if (hallYellowState == hallBlueState) {
      hallBlueState ^= 1;
    } else if (hallBlueState == hallGreenState) {
      hallGreenState ^= 1;
    } else if (hallGreenState == hallYellowState) {
      hallYellowState ^= 1;
    }
  }
  if (!applyMask || maskStateHigh) {
    digitalWrite(hallYellowPin, hallYellowState);
    digitalWrite(hallBluePin, hallBlueState);
    digitalWrite(hallGreenPin, hallGreenState);
  } else {
    digitalWrite(hallYellowPin, LOW);
    digitalWrite(hallBluePin, LOW);
    digitalWrite(hallGreenPin, LOW);
  }
}

/***
  * A protothread helper function calls hallSingGen after 'interval' microseconds passed
  */
static int ptHallSingGen(struct pt *pt, unsigned long interval) {
  static unsigned long timestamp = 0;
  if (timestamp > micros()) timestamp = micros();
  PT_BEGIN(pt);
  while(1) {
    PT_WAIT_UNTIL(pt, micros() - timestamp > interval );
    timestamp = micros();
    hallSingGen();
  }
  PT_END(pt);
}

/***
  * Simple speed indicators
  */
void blink() {
  bool ledstate = digitalRead(ledPin);
  ledstate ^= 1;
  digitalWrite(ledPin, ledstate);
  blinkLenght = (long)1000000 - (long)abs(speed) * 9000;
}

/***
 * A protothread helper function calls blink after 'interval' microseconds passed
 */
static int ptBlink(struct pt *pt, unsigned long interval) {
  static unsigned long timestamp = 0;
  if (timestamp > micros()) timestamp = micros();
  PT_BEGIN(pt);
  while(1) {
    PT_WAIT_UNTIL(pt, micros() - timestamp > interval );
    timestamp = micros();
    blink();
  }
  PT_END(pt);
}

/***
  * The bottom flattened sine wave signal generator
  */
void waveGen() {
  static int phase = 0;
  maskStateHigh = ++phase % 3 == 0;
  digitalWrite(waveGenPin, maskStateHigh);
  if (applyMask) {
    if (maskStateHigh) {
      digitalWrite(hallYellowPin, hallYellowState);
      digitalWrite(hallBluePin, hallBlueState);
      digitalWrite(hallGreenPin, hallGreenState);
    } else {
      digitalWrite(hallYellowPin, LOW);
      digitalWrite(hallBluePin, LOW);
      digitalWrite(hallGreenPin, LOW);
    }
  }
}

/***
  * A protothread helper function calls waveGen after 'interval' microseconds passed
  */
static int ptWaveGen(struct pt *pt, unsigned long interval) {
  static unsigned long timestamp = 0;
  if (timestamp > micros()) timestamp = micros();
  PT_BEGIN(pt);
  while(1) {
    PT_WAIT_UNTIL(pt, micros() - timestamp > interval );
    timestamp = micros();
    waveGen();
  }
  PT_END(pt);
}

/***
  * Well tested rotary encoder.
  */
void readRotaryEnc() {
  static unsigned long timestamp = 0;
  bool rotaryCLKState = digitalRead(rotaryEncCLKPin);
  if (!rotaryCLKState && (timestamp+500) < micros()) {
    if (digitalRead(rotaryEncDTPin)) {
      if (speed > -maxSpeed) speed --;
    } else {
      if (speed < maxSpeed) speed ++;
    }
    if (speed != 0) hallSignLength = (long)1000000 / (abs(speed) * 6);
    else hallSignLength = 1000000;
  }
  timestamp = micros();
}

/***
 * Serial debugger about frequency, speed and settings
 */
void debugInfo() {
  Serial.print("f [Hz]: ");
  Serial.println(speed);
  Serial.print("t [us]: ");
  Serial.println(hallSignLength);
  Serial.print("M: ");
  Serial.println(applyMask);
}
/***
  * A protothread helper function calls debugInfo after 'interval' microseconds passed
  */
static int ptDebugInfo(struct pt *pt, unsigned long interval) {
  static unsigned long timestamp = 0;
  if (timestamp > micros()) timestamp = micros();
  PT_BEGIN(pt);
  while(1) {
    PT_WAIT_UNTIL(pt, micros() - timestamp > interval );
    timestamp = micros();
    debugInfo();
  }
  PT_END(pt);
}

void setup() {
  PT_INIT(&pt1);
  PT_INIT(&pt2);
  PT_INIT(&pt3);
  PT_INIT(&pt4);
  PT_INIT(&pt5);

  if (_SERIAL_DEBUG) {
    Serial.begin(_SERIAL_DEBUG);
    Serial.println("Hello FakeHall!");
  }

  pinMode(rotaryEncCLKPin, INPUT);
  pinMode(rotaryEncDTPin, INPUT);
  attachInterrupt (digitalPinToInterrupt(rotaryEncCLKPin),readRotaryEnc,FALLING);

  pinMode(ledPin, OUTPUT);
  pinMode(waveGenPin, OUTPUT);

  pinMode(hallYellowPin, OUTPUT);
  pinMode(hallBluePin, OUTPUT);
  pinMode(hallGreenPin, OUTPUT);

  pinMode(waveMaskSWPin, INPUT_PULLUP);
  pinMode(rotaryEncSWPin, INPUT_PULLUP);
  maskSWLastState = digitalRead(waveMaskSWPin);
  rotarySWLastState = digitalRead(rotaryEncSWPin);
}

void loop () {
  if (_SERIAL_DEBUG) ptDebugInfo(&pt1, 2000000);
  ptWaveGen(&pt2, 6667); //150Hz
  ptHallSingGen(&pt3, hallSignLength);
  ptBlink(&pt4, blinkLenght);
  ptCheckSwitches(&pt5, 5000);
}

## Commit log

2018-05-16 Carone minimal viable code is done. Although need to be tested with the board on testing-bench
2018-06-18 Created hall signal faker
2018-06-25 Fix the intro and add remark about wrong initial measurement
    [fakehall.ino]
2018-06-26 Added hall effect sensor and counter. Removed the controller logic keep only core fetures
2018-07-25 Removed protothread library and re-purpose the code to work as an etension board
2018-07-25 Upgraded the UART library
2018-08-04 Proof of cencept for software error correction of hall efect sensor. Plus code re-org
    [carone.ino]
2018-08-06 Software correction of hall effect sensor works well :) no need schmitt trigger
    [carone.ino]
2018-08-06 Added Fritzing
    [carone-v4.fzz]
2018-08-18 added i2c support
2018-11-16 Fixed I2C settings. Looking for solve the I2C vs Software Serial conflict
    [carone.ino]
2018-11-19 added button test
2018-12-27 I had a compiler issue, so I put the include to the beginning of the file and it solved
    [carone.ino]
2018-12-29 Added hack to avoid a bug in the board and generally improve behaviour based on experience
    [caronebuttons.ino]
2019-01-02 Experiments with analog hall effect processing
2019-02-03 Tested the new hall effect detection and processing. OK
2019-02-05 Added accelerometer
2019-02-07 Tested Auto-cruise algorithm. Improved documentation. Fixed schem.
    [carone-v4.fzz]
2019-02-07 Added wireing section to doc
2019-02-08 Added hardware description with Fritzing project to documentation
    [data-selector-v3.fzz]
